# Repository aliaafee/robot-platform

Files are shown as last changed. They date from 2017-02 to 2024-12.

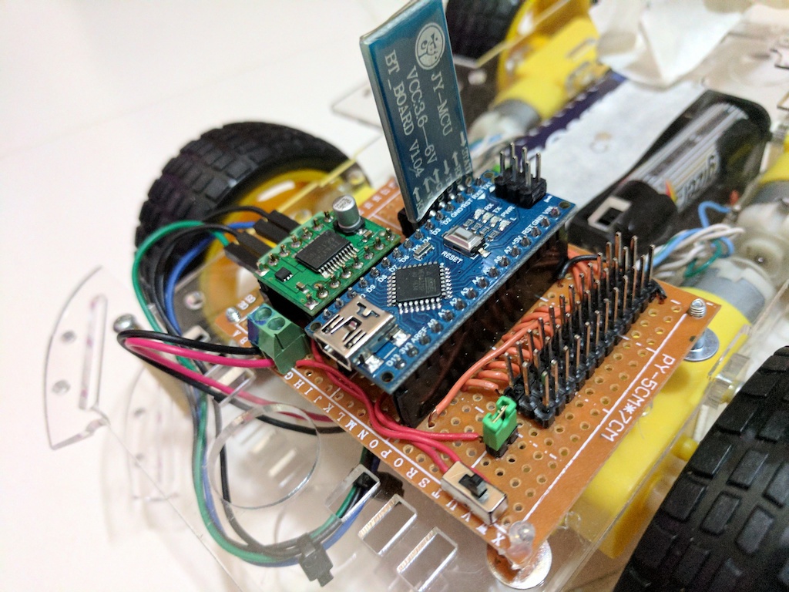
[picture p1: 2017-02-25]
photos/robot-platform.jpg

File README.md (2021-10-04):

# Robot Platform

An arduino based wheeled robot platform.

18650 battery holder

protection circuite
holder for two

2S 20A 7.4V w/Balance Lithium Li-ion 18650 Battery BMS Pack Protection PCB Board

LM2596 DC-DC Buck Converter Step Down Adjustable Power Supply Module

B0505S circuit isolator DC-DC converter

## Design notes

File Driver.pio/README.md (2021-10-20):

# Driver.pio

Firmware for robot driver.

TODO: Implement this as a finite state machine.
see http://robotics.sk/go/FSM/finite-state-automata.pdf

## Functions

Robot driver recieves commands over I2C bus(acts as I2C slave).
Performs basic functions such as movement and collision detection.
Acts as a state machine.

Example: when given command "move by x steps forward", 
sets internal state to "moving forward",
sets motor controller to move forwards,
starts counting steps using wheel encoder interrupts,
stops the motor and sets state to "stopped" when steps goal reached.
During this process robot driver is able to send status via I2C bus when
master makes a request. Robot driver also looks for collisions and stops
when collision detected and updates state appropriately and also sets an
error state.

## Build and Upload

* Install PlatformIO
* Install required depenencies `pio lib install`
* Update `board` and `upload_port` to appropriate values in `platformio.ini`
* Build `pio run`
* Upload to device `pio run -t upload`

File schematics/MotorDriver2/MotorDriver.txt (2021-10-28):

"Source:"	"/home/ali/Projects/robot-platform/schematics/MotorDriver2/MotorDriver.sch"
"Date:"	"Thu 28 Oct 2021 21:13:58 +0545"
"Tool:"	"Eeschema 5.1.10"
"Component Count:"	"37"
"Ref"	"Value"	"Part"	"Footprint"	"Description"	"Vendor"
"C1"	"10uF"	"Device:CP"	"Capacitor_SMD:CP_Elec_4x5.4"	"Polarized capacitor"	""
"C2"	"15pF"	"Device:C"	"Capacitor_SMD:C_1206_3216Metric"	"Unpolarized capacitor"	""
"C3"	"0.1uF"	"Device:C"	"Capacitor_SMD:C_1206_3216Metric"	"Unpolarized capacitor"	""
"C4"	"15pF"	"Device:C"	"Capacitor_SMD:C_1206_3216Metric"	"Unpolarized capacitor"	""
"C5"	"10uF"	"Device:CP"	"Capacitor_SMD:CP_Elec_4x5.4"	"Polarized capacitor"	""
"C6"	"0.1uF"	"Device:C"	"Capacitor_SMD:C_1206_3216Metric"	"Unpolarized capacitor"	""
"C7"	"0.1uF"	"Device:C"	"Capacitor_SMD:C_1206_3216Metric"	"Unpolarized capacitor"	""
"C8"	"0.1uf"	"Device:C"	"Capacitor_SMD:C_1206_3216Metric"	"Unpolarized capacitor"	""
"C9"	"10uf"	"Device:CP"	"Capacitor_SMD:CP_Elec_4x5.4"	"Polarized capacitor"	""
"C10"	"10uf"	"Device:CP"	"Capacitor_SMD:CP_Elec_4x5.4"	"Polarized capacitor"	""
"C11"	"0.1uf"	"Device:C"	"Capacitor_SMD:C_1206_3216Metric"	"Unpolarized capacitor"	""
"D1"	"RED"	"Device:LED"	"Diode_SMD:D_1206_3216Metric"	"Light emitting diode"	""
"D2"	"GREEN"	"Device:LED"	"Diode_SMD:D_1206_3216Metric"	"Light emitting diode"	""
"H1"	"MountingHole"	"Mechanical:MountingHole"	"MountingHole:MountingHole_2.5mm"	"Mounting Hole without connection"	""
"H2"	"MountingHole"	"Mechanical:MountingHole"	"MountingHole:MountingHole_2.5mm"	"Mounting Hole without connection"	""
"H3"	"MountingHole"	"Mechanical:MountingHole"	"MountingHole:MountingHole_2.5mm"	"Mounting Hole without connection"	""
"H4"	"MountingHole"	"Mechanical:MountingHole"	"MountingHole:MountingHole_2.5mm"	"Mounting Hole without connection"	""
"J1"	"9Vin"	"Connector_Generic:Conn_01x02"	"Connector_JST:JST_XH_B2B-XH-A_1x02_P2.50mm_Vertical"	"Generic connector, single row, 01x02, script generated (kicad-library-utils/schlib/autogen/connector/)"	""
"J2"	"ICSP"	"Connector_Generic:Conn_02x03_Odd_Even"	"Connector_PinHeader_2.54mm:PinHeader_2x03_P2.54mm_Vertical"	"Generic connector, double row, 02x03, odd/even pin numbering scheme (row 1 odd numbers, row 2 even numbers), script generated (kicad-library-utils/schlib/autogen/connector/)"	""
"J3"	"FTDI"	"Connector_Generic:Conn_01x06"	"Connector_PinHeader_2.54mm:PinHeader_1x06_P2.54mm_Vertical"	"Generic connector, single row, 01x06, script generated (kicad-library-utils/schlib/autogen/connector/)"	""
"J4"	"I2C"	"Connector_Generic:Conn_01x04"	"Connector_JST:JST_XH_B4B-XH-A_1x04_P2.50mm_Vertical"	"Generic connector, single row, 01x04, script generated (kicad-library-utils/schlib/autogen/connector/)"	""
"J5"	"3v3out"	"Connector_Generic:Conn_01x02"	"Connector_JST:JST_XH_B2B-XH-A_1x02_P2.50mm_Vertical"	"Generic connector, single row, 01x02, script generated (kicad-library-utils/schlib/autogen/connector/)"	""
"J6"	"AnalogPins"	"Connector_Generic:Conn_02x03_Odd_Even"	"Connector_PinHeader_2.54mm:PinHeader_2x03_P2.54mm_Vertical"	"Generic connector, double row, 02x03, odd/even pin numbering scheme (row 1 odd numbers, row 2 even numbers), script generated (kicad-library-utils/schlib/autogen/connector/)"	""
"J7"	"WheelEncA"	"Connector_Generic:Conn_01x03"	"Connector_JST:JST_XH_B3B-XH-A_1x03_P2.50mm_Vertical"	"Generic connector, single row, 01x03, script generated (kicad-library-utils/schlib/autogen/connector/)"	""
"J8"	"WheelEncB"	"Connector_Generic:Conn_01x03"	"Connector_JST:JST_XH_B3B-XH-A_1x03_P2.50mm_Vertical"	"Generic connector, single row, 01x03, script generated (kicad-library-utils/schlib/autogen/connector/)"	""
"J9"	"MotorA"	"Connector_Generic:Conn_01x02"	"Connector_JST:JST_XH_B2B-XH-A_1x02_P2.50mm_Vertical"	"Generic connector, single row, 01x02, script generated (kicad-library-utils/schlib/autogen/connector/)"	""
"J10"	"MotorB"	"Connector_Generic:Conn_01x02"	"Connector_JST:JST_XH_B2B-XH-A_1x02_P2.50mm_Vertical"	"Generic connector, single row, 01x02, script generated (kicad-library-utils/schlib/autogen/connector/)"	""
"R1"	"10k"	"Device:R"	"Resistor_SMD:R_1206_3216Metric"	"Resistor"	""
"R2"	"10k"	"Device:R"	"Resistor_SMD:R_1206_3216Metric"	"Resistor"	""
"R3"	"10k"	"Device:R"	"Resistor_SMD:R_1206_3216Metric"	"Resistor"	""
"R4"	"10k"	"Device:R"	"Resistor_SMD:R_1206_3216Metric"	"Resistor"	""
"R5"	"330"	"Device:R"	"Resistor_SMD:R_1206_3216Metric"	"Resistor"	""
"SW1"	"Reset"	"Switch:SW_Push"	"Button_Switch_SMD:SW_SPST_B3U-1000P-B"	"Push button switch, generic, two pins"	""
"U1"	"ATmega328P-MU"	"MCU_Microchip_ATmega:ATmega328P-MU"	"Package_DFN_QFN:QFN-32-1EP_5x5mm_P0.5mm_EP3.1x3.1mm"	"20MHz, 32kB Flash, 2kB SRAM, 1kB EEPROM, QFN-32"	""
"U2"	"MIC5205-3.3YM5"	"Regulator_Linear:MIC5205-3.3YM5"	"Package_TO_SOT_SMD:SOT-23-5"	"150mA low dropout linear regulator, fixed 3.3V output, SOT-23-5"	""
"U3"	"TB6612FNG"	"Driver_Motor:TB6612FNG"	"Package_SO:SSOP-24_5.3x8.2mm_P0.65mm"	"Driver IC for Dual DC motor, SSOP-24"	""
"Y1"	"HC-49SM16MHz20pF30ppm"	"Device:Crystal"	"Crystal:Crystal_SMD_HC49-SD"	"Two pin crystal"	""

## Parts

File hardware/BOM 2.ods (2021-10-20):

# | Desc | Qty | Unit Price | Price | Exclude | Remaining | Details
Power
1 | ICR 18650 Cell (Samsung) | 2 | 7.78 | 15.56 |  | 15.56
2 | 18650 Holder 2 Cell | 1 | 1.22 | 1.22 |  | 1.22
3 | 18650 BMS 2S 3A 7.4V | 1 | 0.42 | 0.42 |  | 0.42
4 | TP5100 Lithium Battery Charge Manager | 1 | 0.57 | 0.57 |  | 0.57
5 | Mini360 DC-DC Step Down Buck Converter | 2 | 0.42 | 0.83 |  | 0.83 | 3.3v and 5v output
6 | MT3608 DC-DC Step Up Boost Converter | 1 | 1.90 | 1.90 |  | 1.90 | 9v out for motor
Robot Driver
1 | Arduino Pro Mini 328 3.3v 8MHz | 1 | 2.69 | 2.69 |  | 2.69 | Brain for driver
2 | USB to TTL Serial Adapter | 1 | 1.21 | 1.21 |  | 1.21 | Programmer for arduino pro mini
3 | TB6612FNG Dual Motor Driver | 1 | 1.30 | 1.30 | 1 | 0.00
4 | HC-02K Speed Sensor Wheel Encoder | 2 | 0.97 | 1.94 |  | 1.94 | *Not needed if chassis available
5 | TCRT5000 Infrared Reflectance Sensor Analog | 4 | 0.71 | 2.84 |  | 2.84 | Front, Back, and Edge on Both Side
Robot Control
1 | Raspberry Pi Zero W | 1 | 14.00 | 14.00 | 1 | 0.00
2 | Triple Axis Compass/Magnetometer Module I2C | 1 | 1.61 | 1.61 |  | 1.61 | Direction
3 | Six Axis Gyro/Accelerometer Module I2C | 1 | 1.41 | 1.41 |  | 1.41 | Orientation
4 | Raspberry Pi Camera | 1 | 29.95 | 29.95 | 1 | 0.00 | Vision
5 | RC Servo – Micro 9G | 2 | 1.98 | 3.96 |  | 3.96 | For Camera Orientation
Robot Chassis
1 | TS100 Metal Tank Chassis with 9v 150rm Motor | 1 | 72.19 | 72.19 |  | 72.19
Communication
1 | 2 Channel I2C Logic Level Converter | 1 | 0.24 | 0.24 |  | 0.24 | For interfacing with 5v devices
Wiring
1 | Stripboard PCB | 3 | 1.40 | 4.20 |  | 4.20
2 | M3 Nylon Standoff kit | 1 | 3.36 | 3.36 |  | 3.36
3 | M3 Brass Standoff kit | 1 | 4.49 | 4.49 |  | 4.49
4 | M2.5 Nylon Standoff kit | 1 | 4.39 | 4.39 |  | 4.39
5 | M2.5 Brass Standoff kit | 1 | 4.99 | 4.99 |  | 4.99
6 | JST XH2.54 Wire Cable Crimmped with Female Plug Pins-4,3,2 | 5 | 0.76 | 3.80 |  | 3.80 | 4pin for I2C, 3pin for Analog/Digital Sensors, 2 pin for Power Delivery
 |  |  |  | 179.07 | Total(USD) | 133.82
 |  |  |  |  | MVR | 2063.5044

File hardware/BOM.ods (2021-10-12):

180Pcs/set M2 M2.5 M3 Hex Head Brass Spacing Screws Threaded Pillar PCB Computer PC Motherboard StandOff Spacer Kit B040
180Pcs/set M2 M2.5 M3 Hex Head Brass Spacing Screws Threaded Pillar PCB Computer PC Motherboard StandOff Spacer Kit B040
200Pcs/set M2 M2.5 M3 M4 Black/White Hex Nylon Standoff Spacer Column Flat Head Nylon Plastic Spacing Screws Nuts
200Pcs/set M2 M2.5 M3 M4 Black/White Hex Nylon Standoff Spacer Column Flat Head Nylon Plastic Spacing Screws Nuts
2SET HC-020K Double Speed Measuring Module to Test Motor's Rotational Speed with Photoelectric Encoders kit
2/4/8 Channel IIC I2C Logic Level Converter Bi-Directional Board Module 2 4 8 Way DC 3.3V/5V With Pins For Arduino Raspberry Pi
5PCS S09 DC-DC Automatic Buck Boost Power Step Up Down Board Module Input 3V-15V Output 3.3V/5V Electronic DIY PCB
5PCS MT3608 DC-DC Step Up Converter Booster Power Supply Module Boost Step-up Board MAX output 28V 2A
5pcs RC Airplane Module Mini 360 DC Buck Converter Step Down Module 4.75V-23V to 1V-17V 17x11x3.8mm New LM2596 2A
TS100 Metal Rc Robot Tank Car Chassis Shock Absorption Car With Suspension System Crawler Caterpillar For Arduino Diy Toy
5 Pcs 6.5x14.5cm Stripboard Veroboard Uncut PCB Platine Single Side Circuit Board
WAVGAT TB6612 DRV8833 Dual Motor Driver 1A TB6612FNG for Arduino Microcontroller Better than L298N
2S 3A 4A 5A 8A 10A 13A 20A 7.4V 8.4V Li-ion 18650 Lithium battery protection board / BMS board Standard / Balance | 18650 2S BMS 3A
1PCS 5V 1A Micro USB 18650 type-c Lithium Battery Charging Board Charger Module+Protection Dual Functions TP4056 18650
1 2 3 4 6 8 x AA High quality DIY Battery Holder Storage Case Box With Switch&Cover for 18650 AA Batteries Standard Container | 18650 size
Raspberry Pi Zero WH
Raspberry Pi NoIR Camera Board
Adjustable Pi Camera Mount
Raspberry Pi Zero v1.3 Camera Cable

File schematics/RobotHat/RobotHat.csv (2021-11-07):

Comment | Designator | Footprint | JLCPCB Part #
100uF | C1 | Capacitor_SMD:CP_Elec_6.3x7.7 | C127971
100nF | C3 | Capacitor_SMD:C_1206_3216Metric | C307331
220uf | C5 | Capacitor_SMD:CP_Elec_6.3x7.7 | C371974
100nF | C6 | Capacitor_SMD:C_1206_3216Metric | C307331
100nF | C7 | Capacitor_SMD:C_1206_3216Metric | C307331
10uf | C8 | Capacitor_SMD:CP_Elec_4x5.3 | C134721
100nF | C9 | Capacitor_SMD:C_1206_3216Metric | C307331
100nF | C10 | Capacitor_SMD:C_1206_3216Metric | C307331
100nF | C11 | Capacitor_SMD:C_1206_3216Metric | C307331
SS34 | D1 | RobotHat:SS34 | C8678
RED | D2 | Diode_SMD:D_0201_0603Metric | C2286
RED | D3 | Diode_SMD:D_0201_0603Metric | C2286
RED | D4 | Diode_SMD:D_0201_0603Metric | C2286
33uH | L1 | RobotHat:YPRH1207-330M | C339951
AO3401A | Q1 | Package_TO_SOT_SMD:SOT-23 | C15127
2N7002 | Q2 | Package_TO_SOT_SMD:SOT-23 | C8545
2N7002 | Q3 | Package_TO_SOT_SMD:SOT-23 | C8545
10k | R3 | Resistor_SMD:R_0201_0603Metric | C25804
330 | R4 | Resistor_SMD:R_0201_0603Metric | C23138
330 | R5 | Resistor_SMD:R_0201_0603Metric | C23138
330 | R6 | Resistor_SMD:R_0201_0603Metric | C23138
10k | R7 | Resistor_SMD:R_0201_0603Metric | C25804
10k | R8 | Resistor_SMD:R_0201_0603Metric | C25804
10k | R9 | Resistor_SMD:R_0201_0603Metric | C25804
10k | R10 | Resistor_SMD:R_0201_0603Metric | C25804
Reset | SW1 | MyFootprints:TS-1187A-B-A-B_PushButton | C318884
ATmega328P-AU | U1 | Package_QFP:TQFP-32_7x7mm_P0.8mm | C14877
LM2596S-5 | U2 | Package_TO_SOT_SMD:TO-263-5_TabPin3 | C194349
TB6612FNG | U3 | Package_SO:SSOP-24_5.3x8.2mm_P0.65mm | C141517
16Mhz | Y1 | RobotHat:CSTCE16M0V53-R0 | C32180

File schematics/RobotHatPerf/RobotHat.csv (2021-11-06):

Comment | Designator | Footprint | JLCPCB Part #
100uF | C1 | Capacitor_SMD:CP_Elec_6.3x7.7 | C127971
22pF | C2 | Capacitor_SMD:C_1206_3216Metric | C12891
22pF | C3 | Capacitor_SMD:C_1206_3216Metric | C12891
100nF | C4 | Capacitor_SMD:C_0402_1005Metric | C307331
220uf | C5 | Capacitor_SMD:CP_Elec_6.3x7.7 | C371974
100nF | C6 | Capacitor_SMD:C_0402_1005Metric | C307331
100nF | C7 | Capacitor_SMD:C_1206_3216Metric | C24497
100nF | C8 | Capacitor_SMD:C_1206_3216Metric | C24497
SS34 | D1 | RobotHat:SS34 | C8678
GREEN | D2 | Diode_SMD:D_0402_1005Metric | C130719
RED | D3 | Diode_SMD:D_0402_1005Metric | C130719
GREEN | D4 | Diode_SMD:D_0402_1005Metric | C130719
33uH | L1 | RobotHat:YPRH1207-330M | C339951
AO3401A | Q1 | Package_TO_SOT_SMD:SOT-23 | C15127
2N7002 | Q2 | Package_TO_SOT_SMD:SOT-23 | C8545
2N7002 | Q3 | Package_TO_SOT_SMD:SOT-23 | C8545
10k | R1 | Resistor_SMD:R_0805_2012Metric | C17724
330 | R3 | Resistor_SMD:R_0402_1005Metric | C25741
330 | R4 | Resistor_SMD:R_0402_1005Metric | C25741
10k | R5 | Resistor_SMD:R_0805_2012Metric | C17724
10k | R6 | Resistor_SMD:R_0805_2012Metric | C17724
10k | R7 | Resistor_SMD:R_0805_2012Metric | C17724
10k | R8 | Resistor_SMD:R_0805_2012Metric | C17724
Reset | SW1 | MyFootprints:TS-1187A-B-A-B_PushButton | C318884
LM2596S-5 | U2 | Package_TO_SOT_SMD:TO-263-5_TabPin3 | C194349

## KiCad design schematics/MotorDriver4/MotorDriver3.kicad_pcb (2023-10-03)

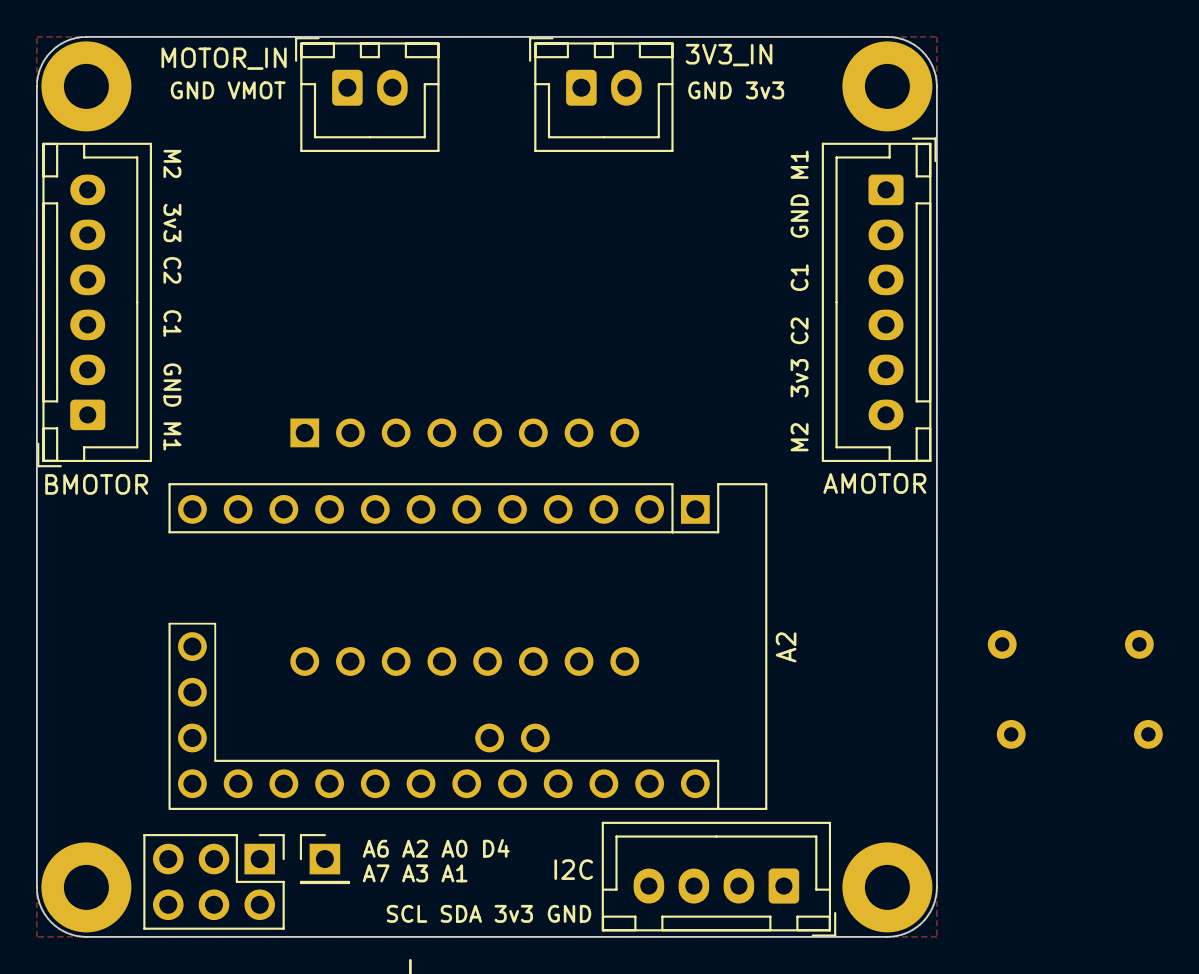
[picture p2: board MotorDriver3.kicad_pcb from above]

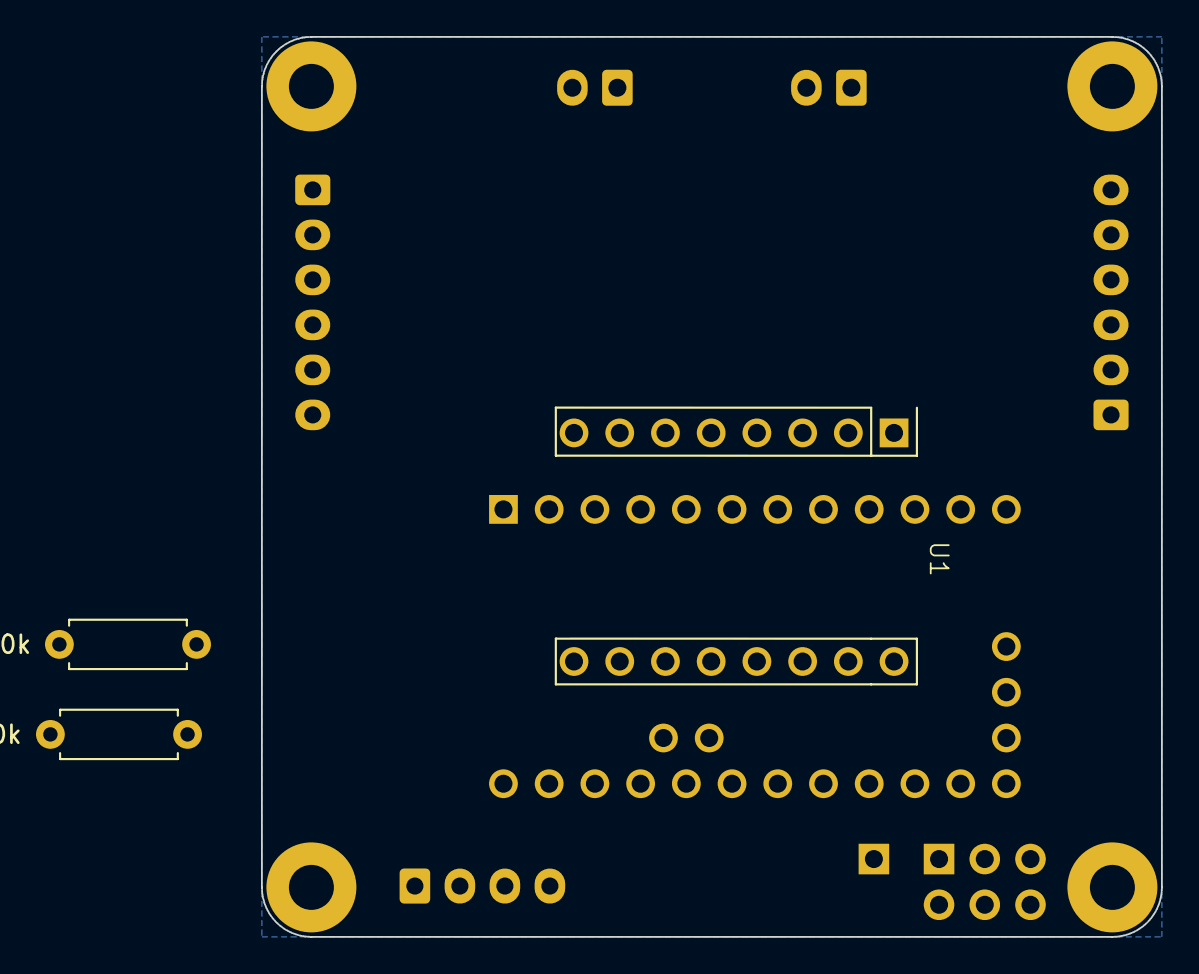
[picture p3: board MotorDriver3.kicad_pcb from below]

Board: 2 copper layers, 50.0 x 50.0 mm, 15 parts (3 on the bottom side), 27 nets, no tracks yet.

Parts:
A2: Arduino_Pro_Mini; Arduino Pro Mini
H1, H2, H3, H4: MountingHole_Pad; MountingHole_2.5mm_Pad
J1: AMOTOR; JST_XH_B6B-XH-A_1x06_P2.50mm_Vertical
J2: BMOTOR; JST_XH_B6B-XH-A_1x06_P2.50mm_Vertical
J3: I2C; JST_XH_B4B-XH-A_1x04_P2.50mm_Vertical
J4: AnalogPins; PinHeader_2x03_P2.54mm_Vertical
J5: MOTOR_IN; JST_XH_B2B-XH-A_1x02_P2.50mm_Vertical
J6: 3V3_IN; JST_XH_B2B-XH-A_1x02_P2.50mm_Vertical
J7: Digital Pins; PinHeader_1x01_P2.54mm_Vertical
R1, R2: 10k; R_Axial_DIN0207_L6.3mm_D2.5mm_P7.62mm_Horizontal
U1: TB6612FNG_Breakout; TB6612FBG_Breakout

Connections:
+3V3: A2.26 (VCC), J1.5, J2.5, J3.2, J6.2, R1.1, R2.1, U1.2 (VCC)
A0: A2.20 (A0), J4.1
A1: A2.21 (A1), J4.2
A2: A2.22 (A2), J4.3
A3: A2.23 (A3), J4.4
A6: A2.14 (A6), J4.5
A7: A2.15 (A7), J4.6
AIN1: A2.10 (D7), U1.15 (AIN2)
AIN2: A2.9 (D6), U1.14 (AIN1)
AINT1: A2.5 (D2), J1.3
AINT2: A2.18 (D12), J1.4
AO1: J1.1, U1.3 (AO1)
AO2: J1.6, U1.4 (AO2)
BIN1: A2.12 (D9), U1.12 (BIN1)
BIN2: A2.16 (D10), U1.11 (BIN2)
BINT1: A2.6 (D3), J2.3
BINT2: A2.19 (D13), J2.4
BO1: J2.1, U1.6 (BO1)
BO2: J2.6, U1.5 (BO2)
D4: A2.7 (D4), J7.1
GND: A2.4 (GND), A2.13 (GND), A2.28 (GND), J1.2, J2.2, J3.1, J5.1, J6.1, U1.1 (GND), U1.8 (GND), U1.9 (GND)
PWMA: A2.8 (D5), U1.16 (PWMA)
PWMB: A2.17 (D11), U1.10 (PWMB)
SCL: A2.25 (A5), J3.4, R1.2
SDA: A2.24 (A4), J3.3, R2.2
STBY: A2.11 (D8), U1.13 (STBY)
VMOT: J5.2, U1.7 (VMOT)

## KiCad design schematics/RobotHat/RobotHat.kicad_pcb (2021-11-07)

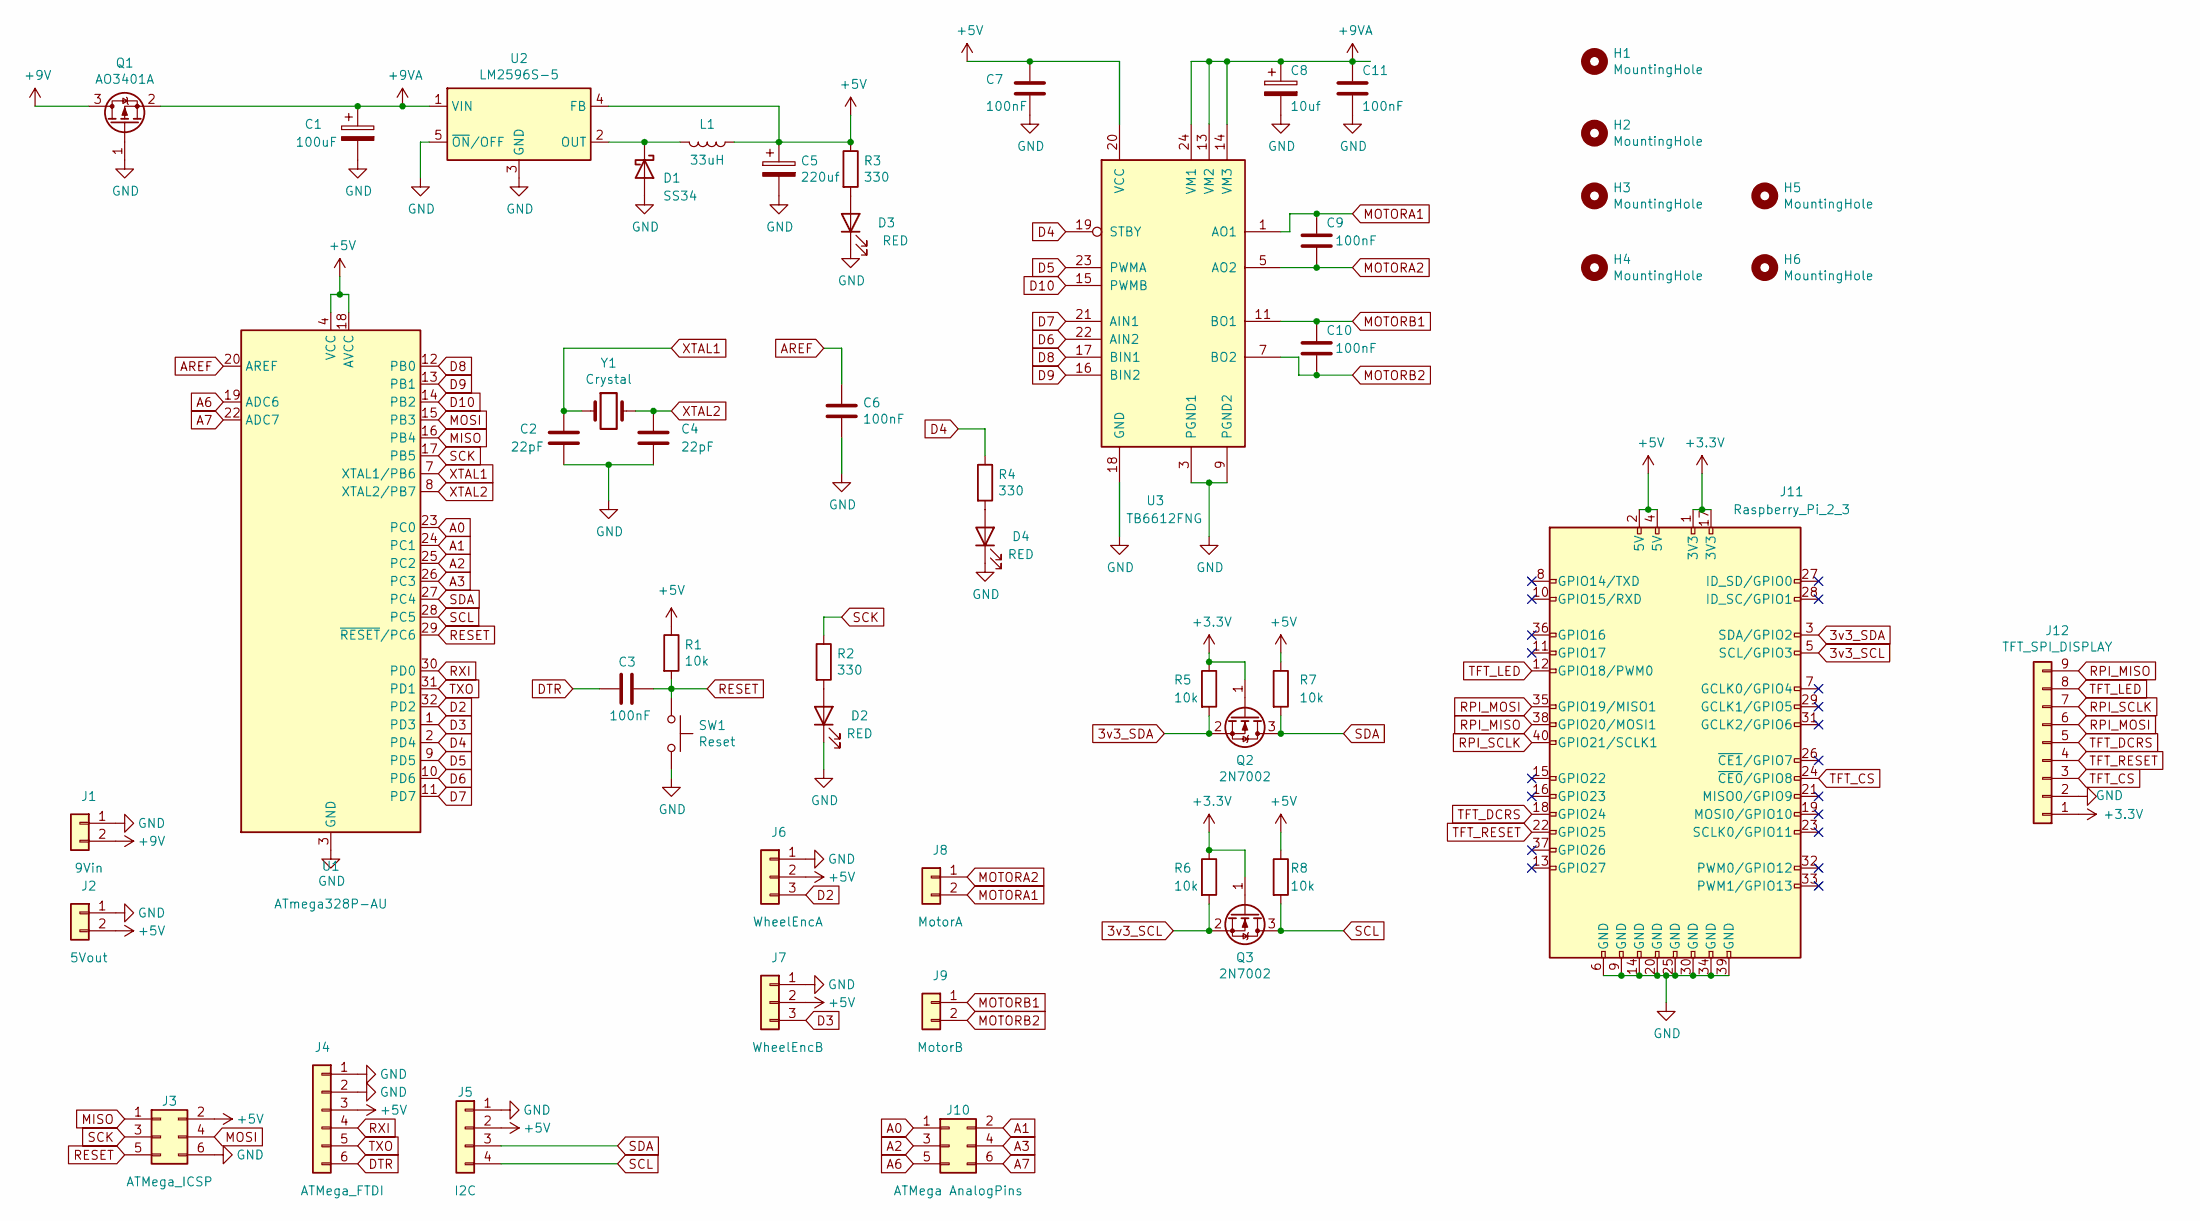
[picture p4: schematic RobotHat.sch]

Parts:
C1: 100uF; CP_Elec_6.3x7.7; Part C127971
C2, C4: 22pF; D_0603_1608Metric; Part C1653
C3, C6, C7, C11: 100nF; C_1206_3216Metric; Part C307331
C5: 220uf; CP_Elec_6.3x7.7; Part C371974
C8: 10uf; CP_Elec_4x5.3; Part C134721
C9, C10: 100nF; C_1206_3216Metric
D1: SS34; Part C8678
D2, D3, D4: RED; D_0603_1608Metric; Part C2286
H1, H2, H3, H4, H5, H6: MountingHole; MountingHole_2.7mm_M2.5_DIN965_Pad
J1: 9Vin; JST_XH_B2B-XH-A_1x02_P2.50mm_Vertical
J2: 5Vout; JST_XH_B2B-XH-A_1x02_P2.50mm_Vertical
J3: ATMega_ICSP; PinHeader_2x03_P2.54mm_Vertical
J4: ATMega_FTDI; PinHeader_1x06_P2.54mm_Horizontal
J5: I2C; JST_XH_B4B-XH-A_1x04_P2.50mm_Vertical
J6: WheelEncA; JST_XH_B3B-XH-A_1x03_P2.50mm_Vertical
J7: WheelEncB; JST_XH_B3B-XH-A_1x03_P2.50mm_Vertical
J8: MotorA; JST_XH_B2B-XH-A_1x02_P2.50mm_Vertical
J9: MotorB; JST_XH_B2B-XH-A_1x02_P2.50mm_Vertical
J10: ATMega AnalogPins; PinSocket_2x03_P2.54mm_Horizontal
J11: Raspberry_Pi_2_3; PinSocket_2x20_P2.54mm_Vertical
J12: TFT_SPI_DISPLAY; PinHeader_2x05_P2.54mm_Vertical
L1: 33uH; YPRH1207-330M; Part C339951
Q1: AO3401A; SOT-23; Part C15127
Q2, Q3: 2N7002; SOT-23; Part C8545
R1, R5, R6, R7, R8: 10k; R_0603_1608Metric; Part C25804
R2, R3, R4: 330; R_0603_1608Metric; Part C23138
SW1: Reset; TS-1187A-B-A-B_PushButton; Part C318884
U1: ATmega328P-AU; TQFP-32_7x7mm_P0.8mm; Part C14877
U2: LM2596S-5; TO-263-5_TabPin3; Part C194349
U3: TB6612FNG; SSOP-24_5.3x8.2mm_P0.65mm; Part C141517
Y1: Crystal; Crystal_HC49-4H_Vertical

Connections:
3v3_SCL: J11.5 (SCL/GPIO3), Q3.2 (S), R6.2
3v3_SDA: J11.3 (SDA/GPIO2), Q2.2 (S), R5.2
+3V3: J11.1 (3V3), J11.17 (3V3), J12.1, Q2.1 (G), Q3.1 (G), R5.1, R6.1
+5V: C5.1, C7.1, J2.2, J3.2, J4.3, J5.2, J6.2, J7.2, J11.2 (5V), J11.4 (5V), L1.1, R1.1, R3.1, R7.1, R8.1, U1.4 (VCC), U1.6 (VCC), U1.18 (AVCC), U2.4 (FB), U3.20 (VCC)
+9V: J1.2, Q1.3 (D)
+9VA: C1.1, C8.1, C11.1, Q1.2 (S), U2.1 (VIN), U3.13 (VM2), U3.14 (VM3), U3.24 (VM1)
A0: J10.1, U1.23 (PC0)
A1: J10.2, U1.24 (PC1)
A2: J10.3, U1.25 (PC2)
A3: J10.4, U1.26 (PC3)
A6: J10.5, U1.19 (ADC6)
A7: J10.6, U1.22 (ADC7)
AREF: C6.2, U1.20 (AREF)
D2: J6.3, U1.32 (PD2)
D3: J7.3, U1.1 (PD3)
D4: R4.1, U1.2 (PD4), U3.19 (STBY)
D5: U1.9 (PD5), U3.23 (PWMA)
D6: U1.10 (PD6), U3.22 (AIN2)
D7: U1.11 (PD7), U3.21 (AIN1)
D8: U1.12 (PB0), U3.17 (BIN1)
D9: U1.13 (PB1), U3.16 (BIN2)
D10: U1.14 (PB2), U3.15 (PWMB)
DTR: C3.1, J4.6
GND: C1.2, C2.2, C4.2, C5.2, C6.1, C7.2, C8.2, C11.2, D1.2 (A), D2.1 (K), D3.1 (K), D4.1 (K), J1.1, J2.1, J3.6, J4.1, J4.2, J5.1, J6.1, J7.1, J11.6 (GND), J11.9 (GND), J11.14 (GND), J11.20 (GND), J11.25 (GND), J11.30 (GND), J11.34 (GND), J11.39 (GND), J12.2, Q1.1 (G), SW1.2, U1.3 (GND), U1.5 (GND), U1.21 (GND), U2.3 (GND), U2.5 (~ON~/OFF), U3.3 (PGND1), U3.4 (PGND1), U3.9 (PGND2), U3.10 (PGND2), U3.18 (GND)
MISO: J3.1, U1.16 (PB4)
MOSI: J3.4, U1.15 (PB3)
MOTORA1: C9.1, J8.2, U3.1 (AO1), U3.2 (AO1)
MOTORA2: C9.2, J8.1, U3.5 (AO2), U3.6 (AO2)
MOTORB1: C10.1, J9.1, U3.11 (BO1), U3.12 (BO1)
MOTORB2: C10.2, J9.2, U3.7 (BO2), U3.8 (BO2)
unnamed: D1.1 (K), L1.2, U2.2 (OUT)
unnamed: D2.2 (A), R2.2
unnamed: D3.2 (A), R3.2
unnamed: D4.2 (A), R4.2
RESET: C3.2, J3.5, R1.2, SW1.1, U1.29 (~RESET~/PC6)
RPI_MISO: J11.38 (GPIO20/MOSI1), J12.9
RPI_MOSI: J11.35 (GPIO19/MISO1), J12.6
RPI_SCLK: J11.40 (GPIO21/SCLK1), J12.7
RXI: J4.4, U1.30 (PD0)
SCK: J3.3, R2.1, U1.17 (PB5)
SCL: J5.4, Q3.3 (D), R8.2, U1.28 (PC5)
SDA: J5.3, Q2.3 (D), R7.2, U1.27 (PC4)
TFT_CS: J11.24 (~CE0~/GPIO8), J12.3
TFT_DCRS: J11.18 (GPIO24), J12.5
TFT_LED: J11.12 (GPIO18/PWM0), J12.8
TFT_RESET: J11.22 (GPIO25), J12.4
TXO: J4.5, U1.31 (PD1)
XTAL1: C2.1, U1.7 (XTAL1/PB6), Y1.1
XTAL2: C4.1, U1.8 (XTAL2/PB7), Y1.2

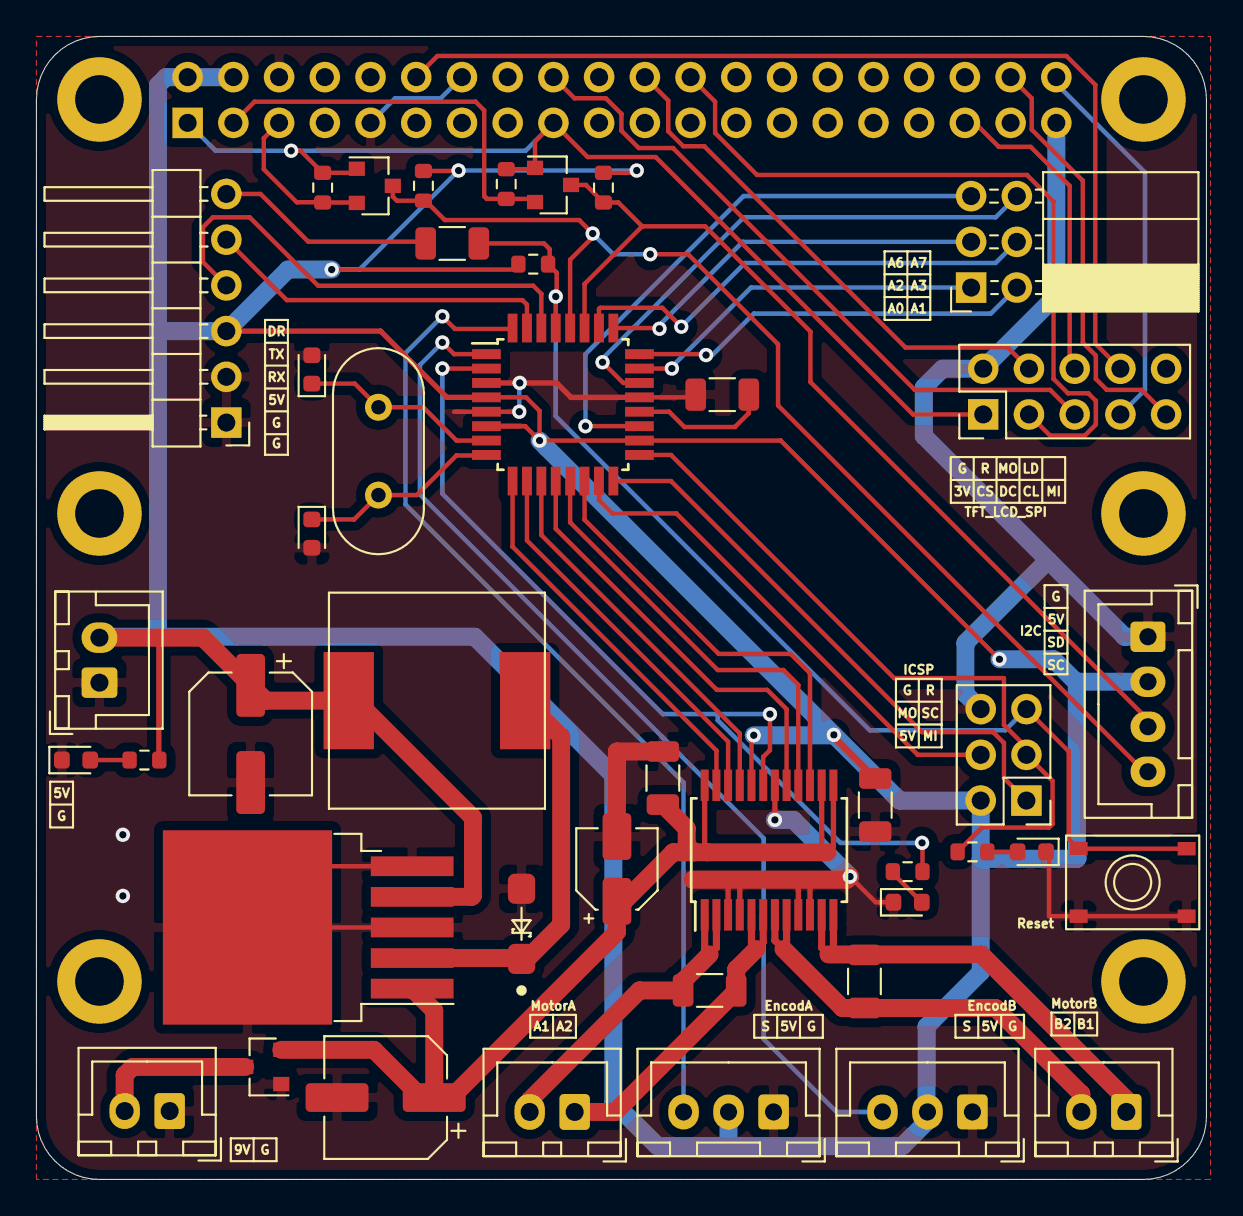
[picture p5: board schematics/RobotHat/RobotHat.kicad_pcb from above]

Board: 2 copper layers, 65.0 x 63.5 mm, 50 parts (1 on the bottom side), 49 nets.

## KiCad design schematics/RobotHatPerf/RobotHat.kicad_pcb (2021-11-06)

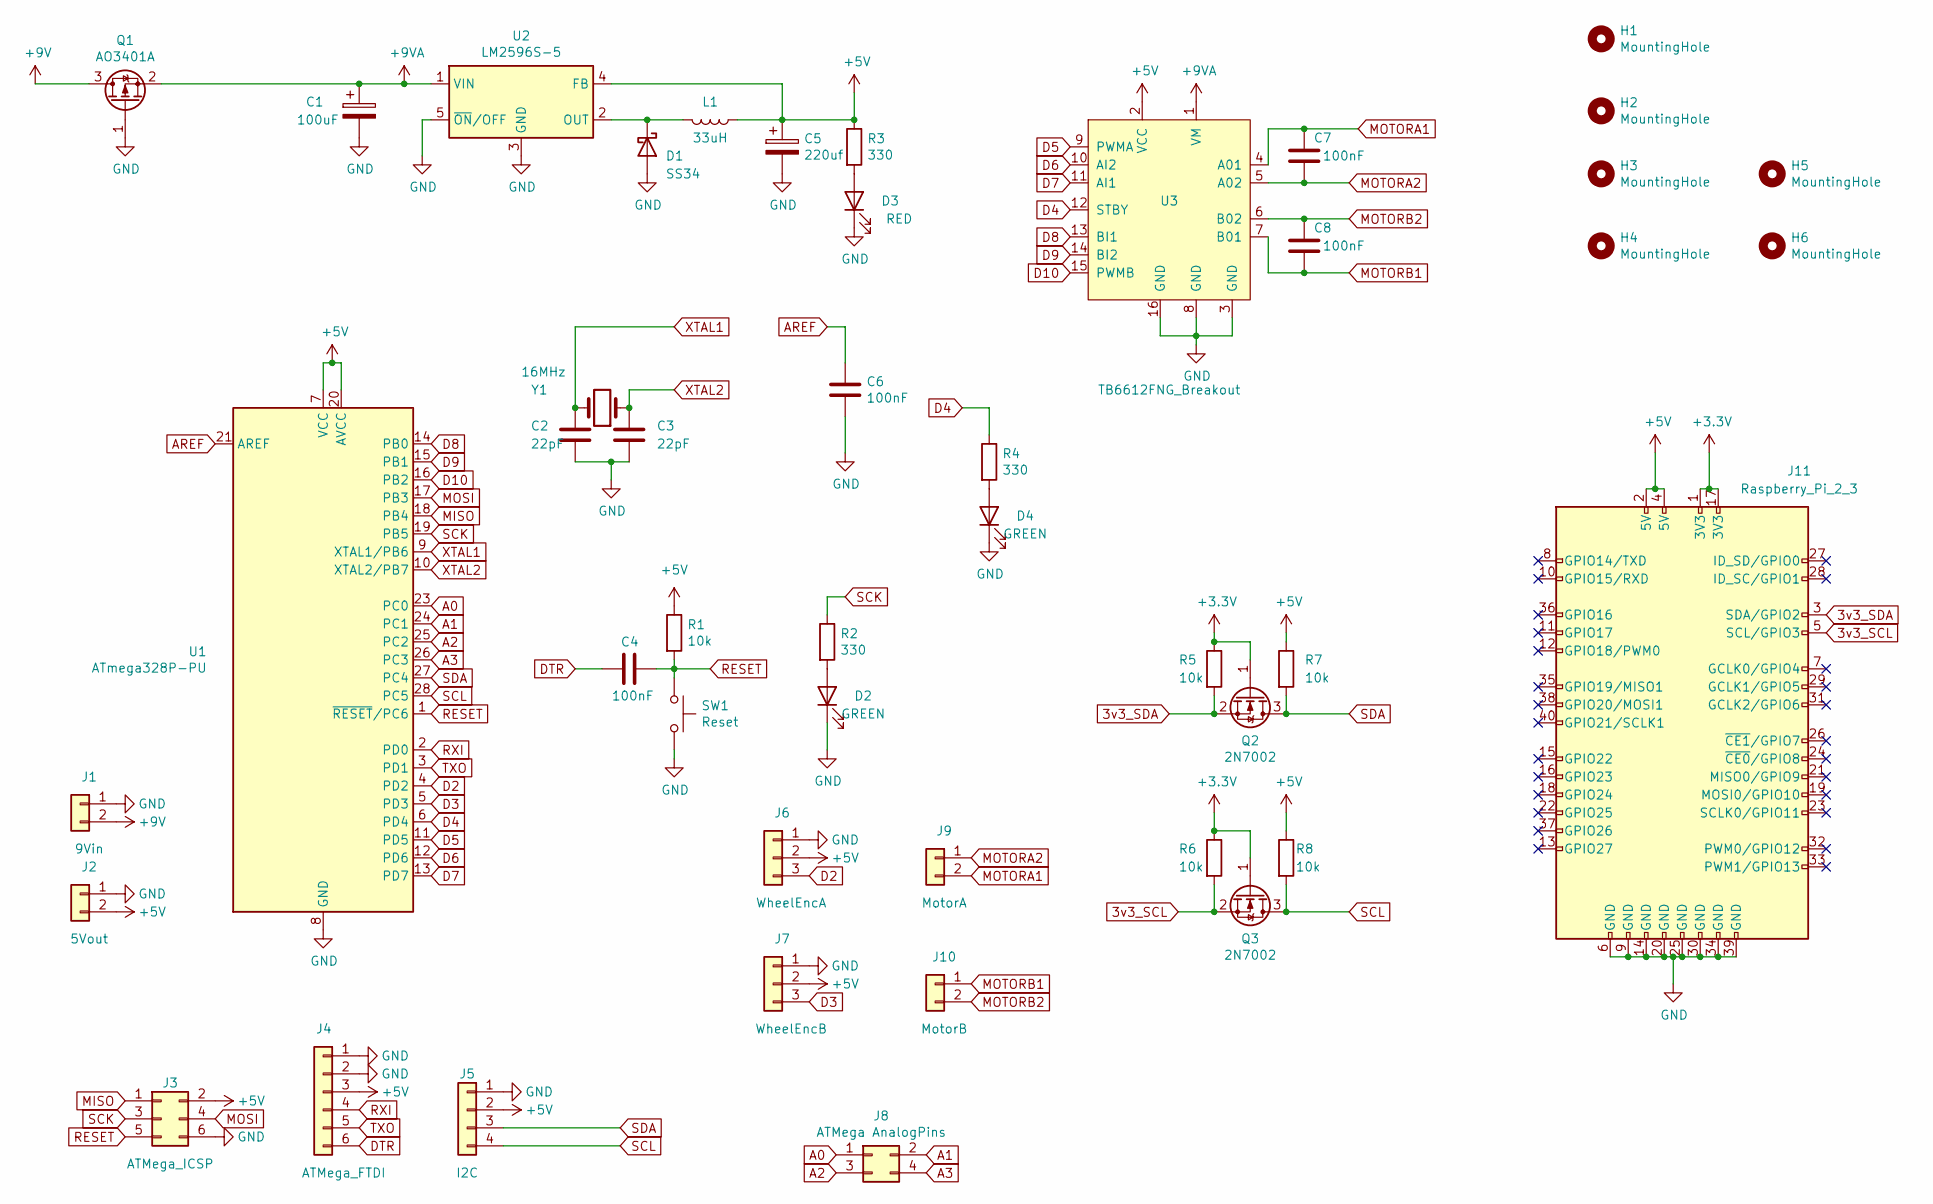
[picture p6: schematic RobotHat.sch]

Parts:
C1: 100uF; CP_Elec_6.3x7.7; Part C127971
C2, C3: 22pF; C_1206_3216Metric; Part C12891
C4, C6: 100nF; C_0402_1005Metric; Part C307331
C5: 220uf; CP_Elec_6.3x7.7; Part C371974
C7, C8: 100nF; C_1206_3216Metric; Part C24497
D1: SS34; Part C8678
D2, D4: GREEN; D_0402_1005Metric; Part C130719
D3: RED; D_0402_1005Metric; Part C130719
H1, H2, H3, H4, H5, H6: MountingHole; MountingHole_2.7mm_M2.5_DIN965_Pad
J1: 9Vin; JST_XH_B2B-XH-A_1x02_P2.50mm_Vertical
J2: 5Vout; JST_XH_B2B-XH-A_1x02_P2.50mm_Vertical
J3: ATMega_ICSP; PinHeader_2x03_P2.54mm_Vertical
J4: ATMega_FTDI; PinHeader_1x06_P2.54mm_Horizontal
J5: I2C; JST_XH_B4B-XH-A_1x04_P2.50mm_Vertical
J6: WheelEncA; JST_XH_B3B-XH-A_1x03_P2.50mm_Vertical
J7: WheelEncB; JST_XH_B3B-XH-A_1x03_P2.50mm_Vertical
J8: ATMega AnalogPins; PinSocket_1x04_P2.54mm_Horizontal
J9: MotorA; JST_XH_B2B-XH-A_1x02_P2.50mm_Vertical
J10: MotorB; JST_XH_B2B-XH-A_1x02_P2.50mm_Vertical
J11: Raspberry_Pi_2_3; PinSocket_2x20_P2.54mm_Vertical
L1: 33uH; YPRH1207-330M; Part C339951
Q1: AO3401A; SOT-23; Part C15127
Q2, Q3: 2N7002; SOT-23; Part C8545
R1, R5, R6, R7, R8: 10k; R_0805_2012Metric; Part C17724
R2, R3, R4: 330; R_0402_1005Metric; Part C25741
SW1: Reset; TS-1187A-B-A-B_PushButton; Part C318884
U1: ATmega328P-PU; DIP-28_W7.62mm
U2: LM2596S-5; TO-263-5_TabPin3; Part C194349
U3: TB6612FNG_Breakout
Y1: 16MHz; Crystal_HC49-U_Vertical

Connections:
3v3_SCL: J11.5 (SCL/GPIO3), Q3.2 (S), R6.2
3v3_SDA: J11.3 (SDA/GPIO2), Q2.2 (S), R5.2
+3V3: J11.1 (3V3), J11.17 (3V3), Q2.1 (G), Q3.1 (G), R5.1, R6.1
+5V: C5.1, J2.2, J3.2, J4.3, J5.2, J6.2, J7.2, J11.2 (5V), J11.4 (5V), L1.1, R1.1, R3.1, R7.1, R8.1, U1.7 (VCC), U1.20 (AVCC), U2.4 (FB), U3.2 (VCC)
+9V: J1.2, Q1.3 (D)
+9VA: C1.1, Q1.2 (S), U2.1 (VIN), U3.1 (VM)
A0: J8.1, U1.23 (PC0)
A1: J8.2, U1.24 (PC1)
A2: J8.3, U1.25 (PC2)
A3: J8.4, U1.26 (PC3)
AREF: C6.2, U1.21 (AREF)
D2: J6.3, U1.4 (PD2)
D3: J7.3, U1.5 (PD3)
D4: R4.1, U1.6 (PD4), U3.12 (STBY)
D5: U1.11 (PD5), U3.9 (PWMA)
D6: U1.12 (PD6), U3.10 (AI2)
D7: U1.13 (PD7), U3.11 (AI1)
D8: U1.14 (PB0), U3.13 (BI1)
D9: U1.15 (PB1), U3.14 (BI2)
D10: U1.16 (PB2), U3.15 (PWMB)
DTR: C4.1, J4.6
GND: C1.2, C2.2, C3.2, C5.2, C6.1, D1.2 (A), D2.1 (K), D3.1 (K), D4.1 (K), J1.1, J2.1, J3.6, J4.1, J4.2, J5.1, J6.1, J7.1, J11.6 (GND), J11.9 (GND), J11.14 (GND), J11.20 (GND), J11.25 (GND), J11.30 (GND), J11.34 (GND), J11.39 (GND), Q1.1 (G), SW1.2, U1.8 (GND), U1.22 (GND), U2.3 (GND), U2.5 (~ON~/OFF), U3.3 (GND), U3.8 (GND), U3.16 (GND)
MISO: J3.1, U1.18 (PB4)
MOSI: J3.4, U1.17 (PB3)
MOTORA1: C7.1, J9.2, U3.4 (A01)
MOTORA2: C7.2, J9.1, U3.5 (A02)
MOTORB1: C8.2, J10.1, U3.7 (B01)
MOTORB2: C8.1, J10.2, U3.6 (B02)
unnamed: D1.1 (K), L1.2, U2.2 (OUT)
unnamed: D2.2 (A), R2.2
unnamed: D3.2 (A), R3.2
unnamed: D4.2 (A), R4.2
RESET: C4.2, J3.5, R1.2, SW1.1, U1.1 (~RESET~/PC6)
RXI: J4.4, U1.2 (PD0)
SCK: J3.3, R2.1, U1.19 (PB5)
SCL: J5.4, Q3.3 (D), R8.2, U1.28 (PC5)
SDA: J5.3, Q2.3 (D), R7.2, U1.27 (PC4)
TXO: J4.5, U1.3 (PD1)
XTAL1: C2.1, U1.9 (XTAL1/PB6), Y1.2
XTAL2: C3.1, U1.10 (XTAL2/PB7), Y1.1

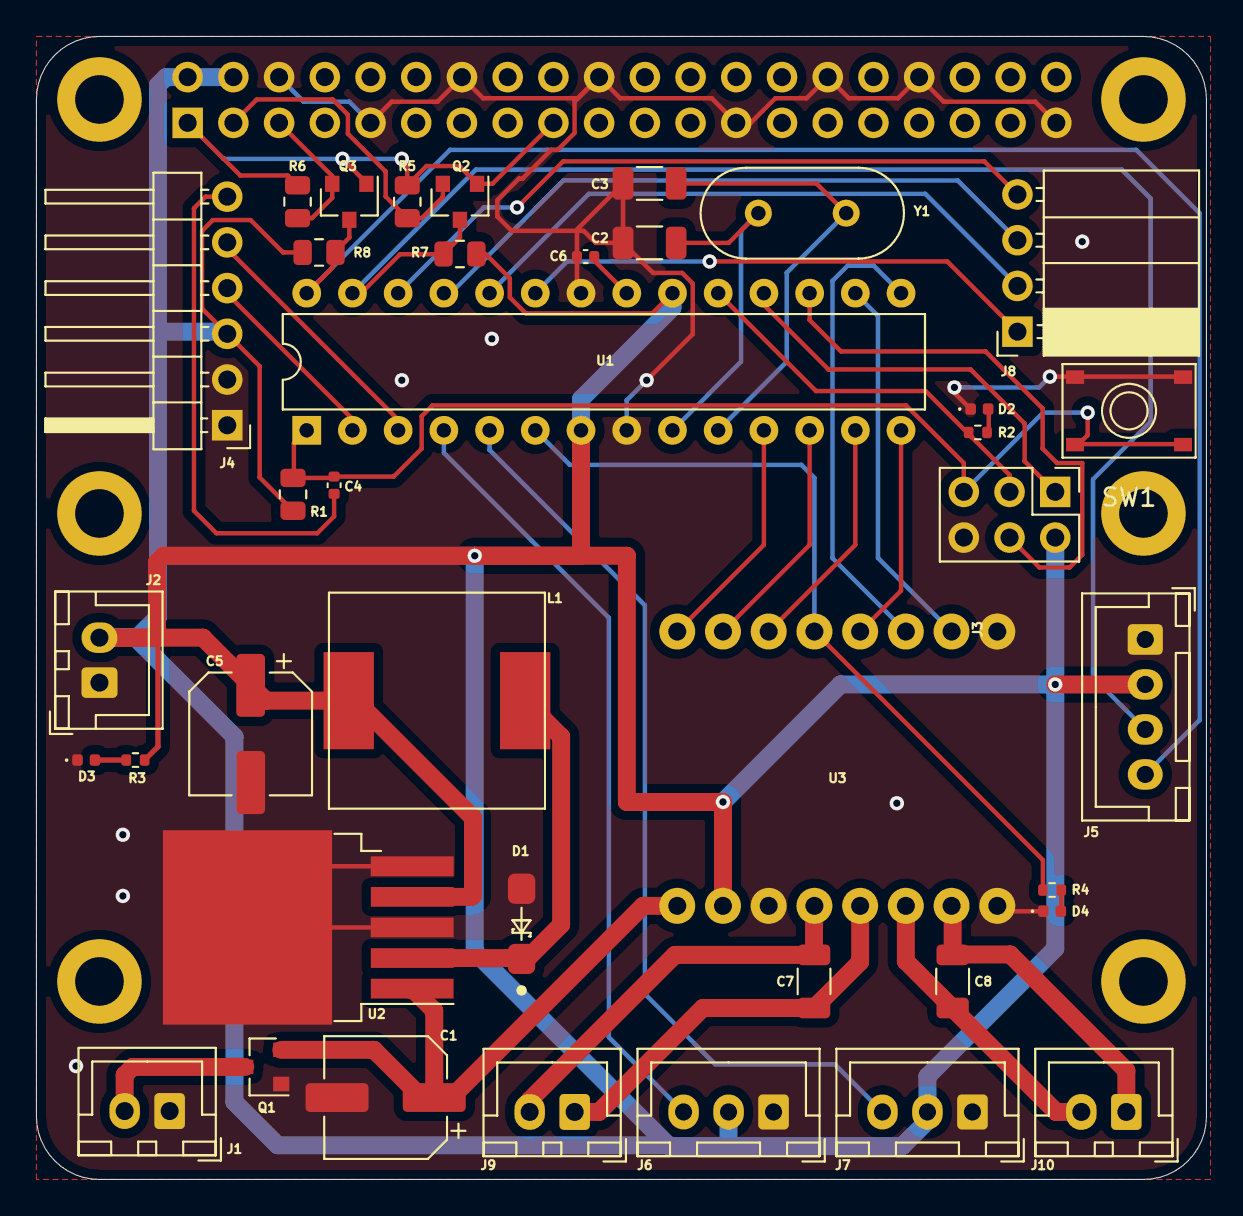
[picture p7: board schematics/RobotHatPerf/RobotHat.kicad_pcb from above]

Board: 2 copper layers, 65.0 x 63.5 mm, 46 parts (1 on the bottom side), 40 nets.

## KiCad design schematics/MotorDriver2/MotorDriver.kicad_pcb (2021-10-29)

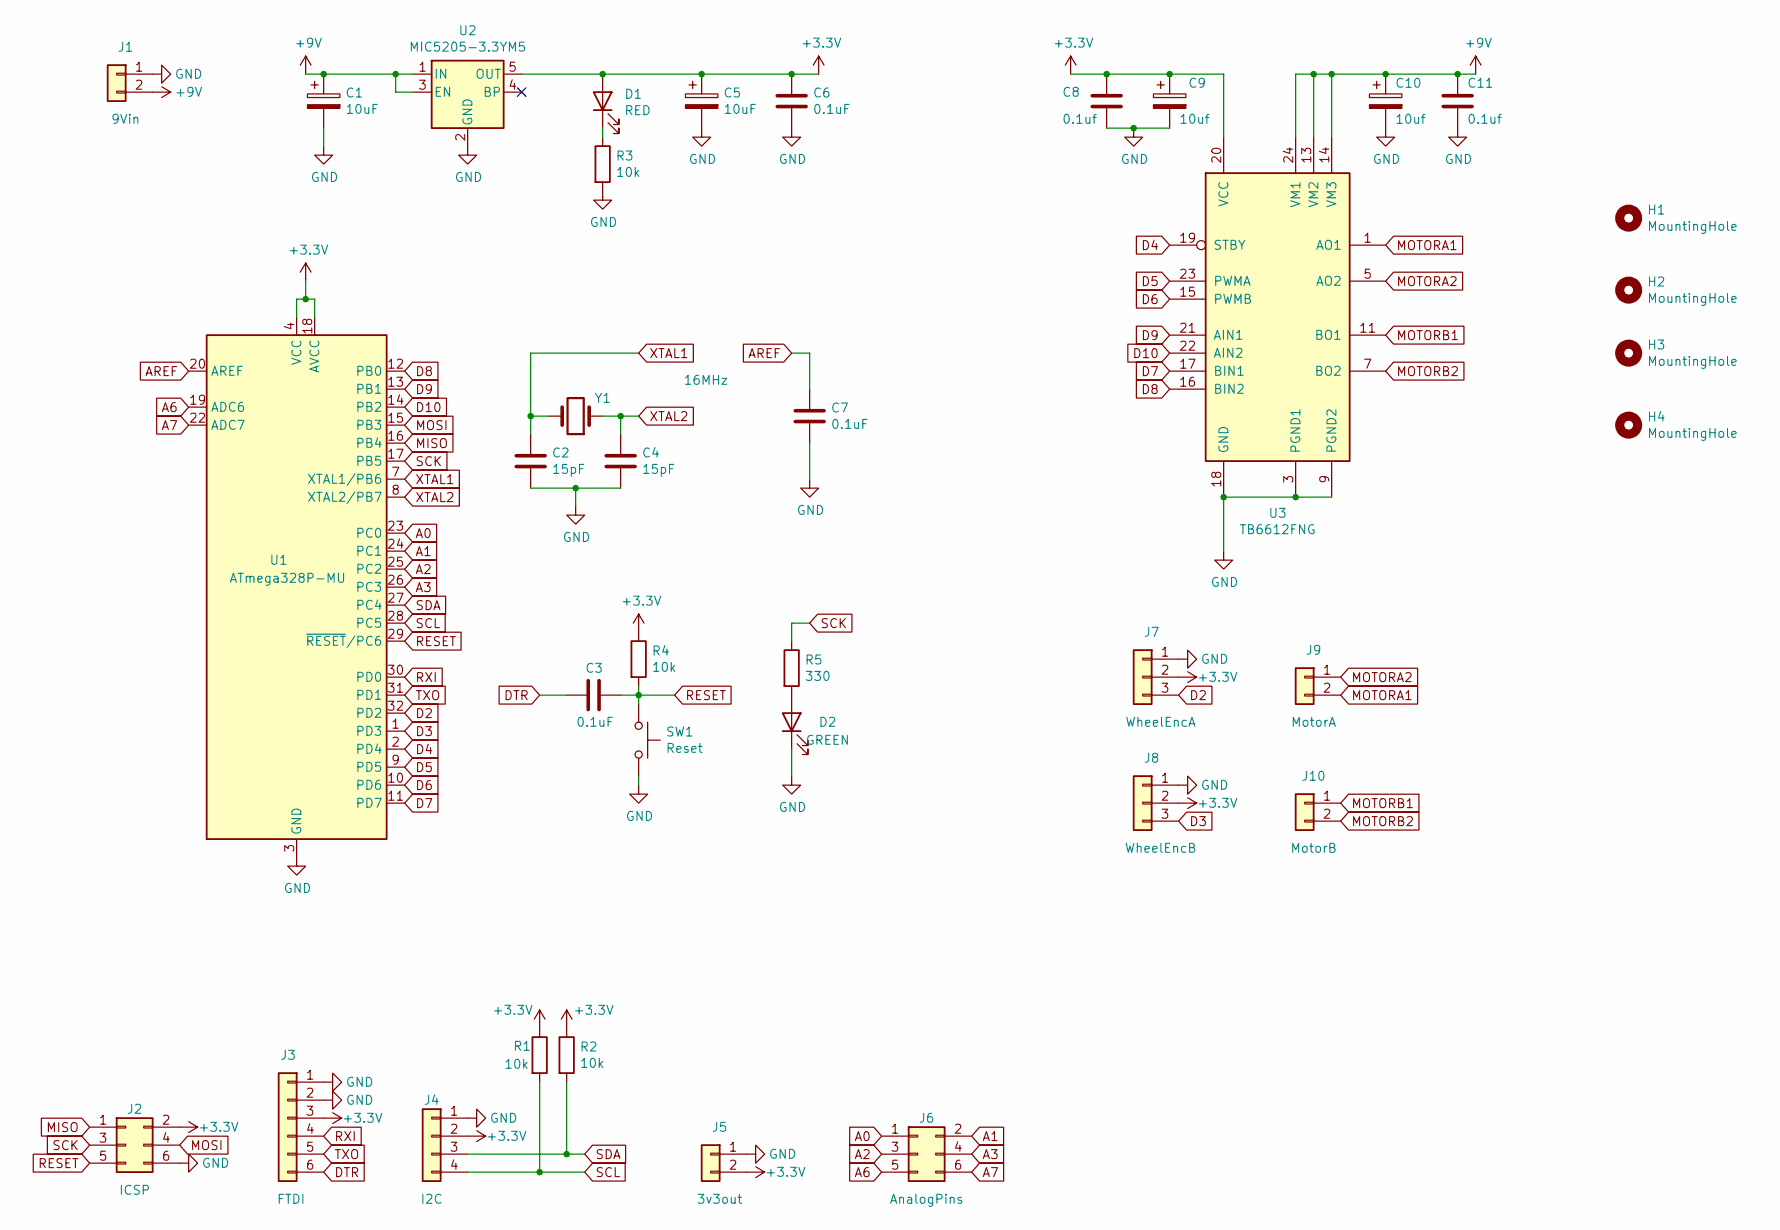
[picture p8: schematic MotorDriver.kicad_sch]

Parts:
C1, C5: 10uF; CP_Elec_4x5.4
C2, C4: 15pF; C_0402_1005Metric
C3, C6, C7: 0.1uF; C_0402_1005Metric
C8, C11: 0.1uf; C_0402_1005Metric
C9, C10: 10uf; CP_Elec_4x5.4
D1: RED; D_0402_1005Metric
D2: GREEN; D_0402_1005Metric
H1, H2, H3, H4: MountingHole; MountingHole_2.5mm
J1: 9Vin; JST_XH_B2B-XH-A_1x02_P2.50mm_Vertical
J2: ICSP; PinHeader_2x03_P2.54mm_Vertical
J3: FTDI; PinHeader_1x06_P2.54mm_Vertical
J4: I2C; JST_XH_B4B-XH-A_1x04_P2.50mm_Vertical
J5: 3v3out; JST_XH_B2B-XH-A_1x02_P2.50mm_Vertical
J6: AnalogPins; PinHeader_2x03_P2.54mm_Vertical
J7: WheelEncA; JST_XH_B3B-XH-A_1x03_P2.50mm_Vertical
J8: WheelEncB; JST_XH_B3B-XH-A_1x03_P2.50mm_Vertical
J9: MotorA; JST_XH_B2B-XH-A_1x02_P2.50mm_Vertical
J10: MotorB; JST_XH_B2B-XH-A_1x02_P2.50mm_Vertical
R1, R2, R3, R4: 10k; R_0402_1005Metric
R5: 330; R_0402_1005Metric
SW1: Reset; SW_SPST_B3U-1000P-B
U1: ATmega328P-MU; QFN-32-1EP_5x5mm_P0.5mm_EP3.1x3.1mm
U2: MIC5205-3.3YM5; SOT-23-5
U3: TB6612FNG; SSOP-24_5.3x8.2mm_P0.65mm
Y1: 16MHz; Crystal_SMD_HC49-SD

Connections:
+3V3: C5.1, C6.1, C8.1, C9.1, D1.2 (A), J2.2, J3.3, J4.2, J5.2, J7.2, J8.2, R1.1, R2.1, R4.1, U1.4 (VCC), U1.6 (VCC), U1.18 (AVCC), U2.5 (OUT), U3.20 (VCC)
+9V: C1.1, C10.1, C11.1, J1.2, U2.1 (IN), U2.3 (EN), U3.13 (VM2), U3.14 (VM3), U3.24 (VM1)
A0: J6.1, U1.23 (PC0)
A1: J6.2, U1.24 (PC1)
A2: J6.3, U1.25 (PC2)
A3: J6.4, U1.26 (PC3)
A6: J6.5, U1.19 (ADC6)
A7: J6.6, U1.22 (ADC7)
AREF: C7.2, U1.20 (AREF)
D2: J7.3, U1.32 (PD2)
D3: J8.3, U1.1 (PD3)
D4: U1.2 (PD4), U3.19 (STBY)
D5: U1.9 (PD5), U3.23 (PWMA)
D6: U1.10 (PD6), U3.15 (PWMB)
D7: U1.11 (PD7), U3.17 (BIN1)
D8: U1.12 (PB0), U3.16 (BIN2)
D9: U1.13 (PB1), U3.21 (AIN1)
D10: U1.14 (PB2), U3.22 (AIN2)
DTR: C3.1, J3.6
GND: C1.2, C2.1, C4.1, C5.2, C6.2, C7.1, C8.2, C9.2, C10.2, C11.2, D2.1 (K), J1.1, J2.6, J3.1, J3.2, J4.1, J5.1, J7.1, J8.1, R3.2, SW1.2, U1.3 (GND), U1.5 (GND), U1.21 (GND), U1.33 (GND), U2.2 (GND), U3.3 (PGND1), U3.4 (PGND1), U3.9 (PGND2), U3.10 (PGND2), U3.18 (GND)
MISO: J2.1, U1.16 (PB4)
MOSI: J2.4, U1.15 (PB3)
MOTORA1: J9.2, U3.1 (AO1), U3.2 (AO1)
MOTORA2: J9.1, U3.5 (AO2), U3.6 (AO2)
MOTORB1: J10.1, U3.11 (BO1), U3.12 (BO1)
MOTORB2: J10.2, U3.7 (BO2), U3.8 (BO2)
unnamed: D1.1 (K), R3.1
unnamed: D2.2 (A), R5.2
RESET: C3.2, J2.5, R4.2, SW1.1, U1.29 (~RESET/PC6)
RXI: J3.4, U1.30 (PD0)
SCK: J2.3, R5.1, U1.17 (PB5)
SCL: J4.4, R1.2, U1.28 (PC5)
SDA: J4.3, R2.2, U1.27 (PC4)
TXO: J3.5, U1.31 (PD1)
XTAL1: C2.2, U1.7 (XTAL1/PB6), Y1.2
XTAL2: C4.2, U1.8 (XTAL2/PB7), Y1.1

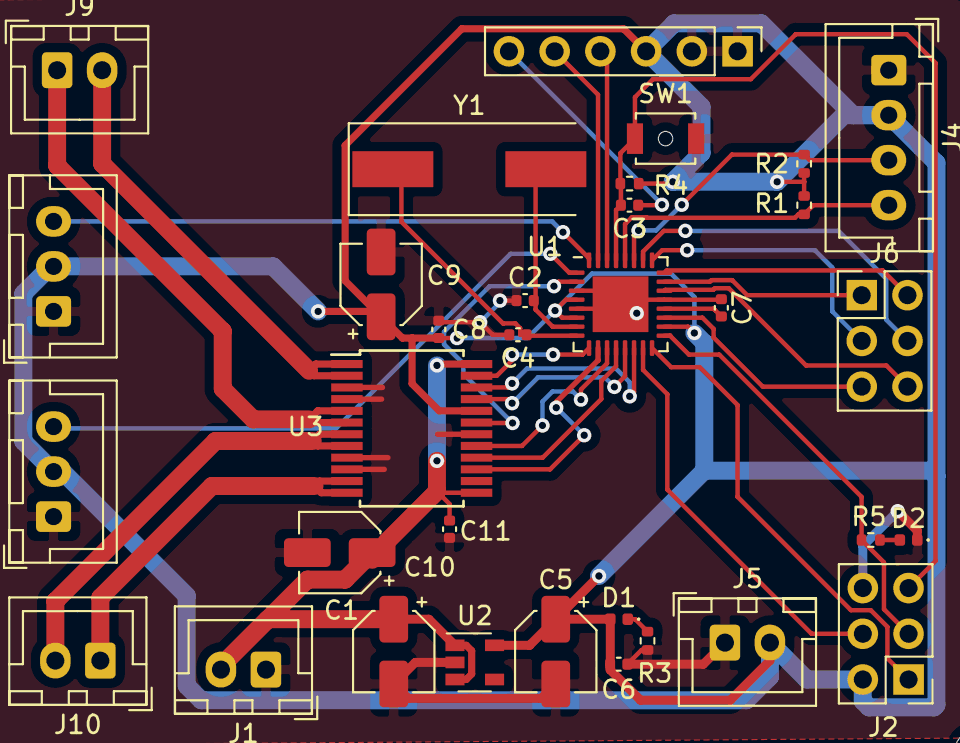
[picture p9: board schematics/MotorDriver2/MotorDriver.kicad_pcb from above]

Board: 2 copper layers, 37 parts (0 on the bottom side), 36 nets.

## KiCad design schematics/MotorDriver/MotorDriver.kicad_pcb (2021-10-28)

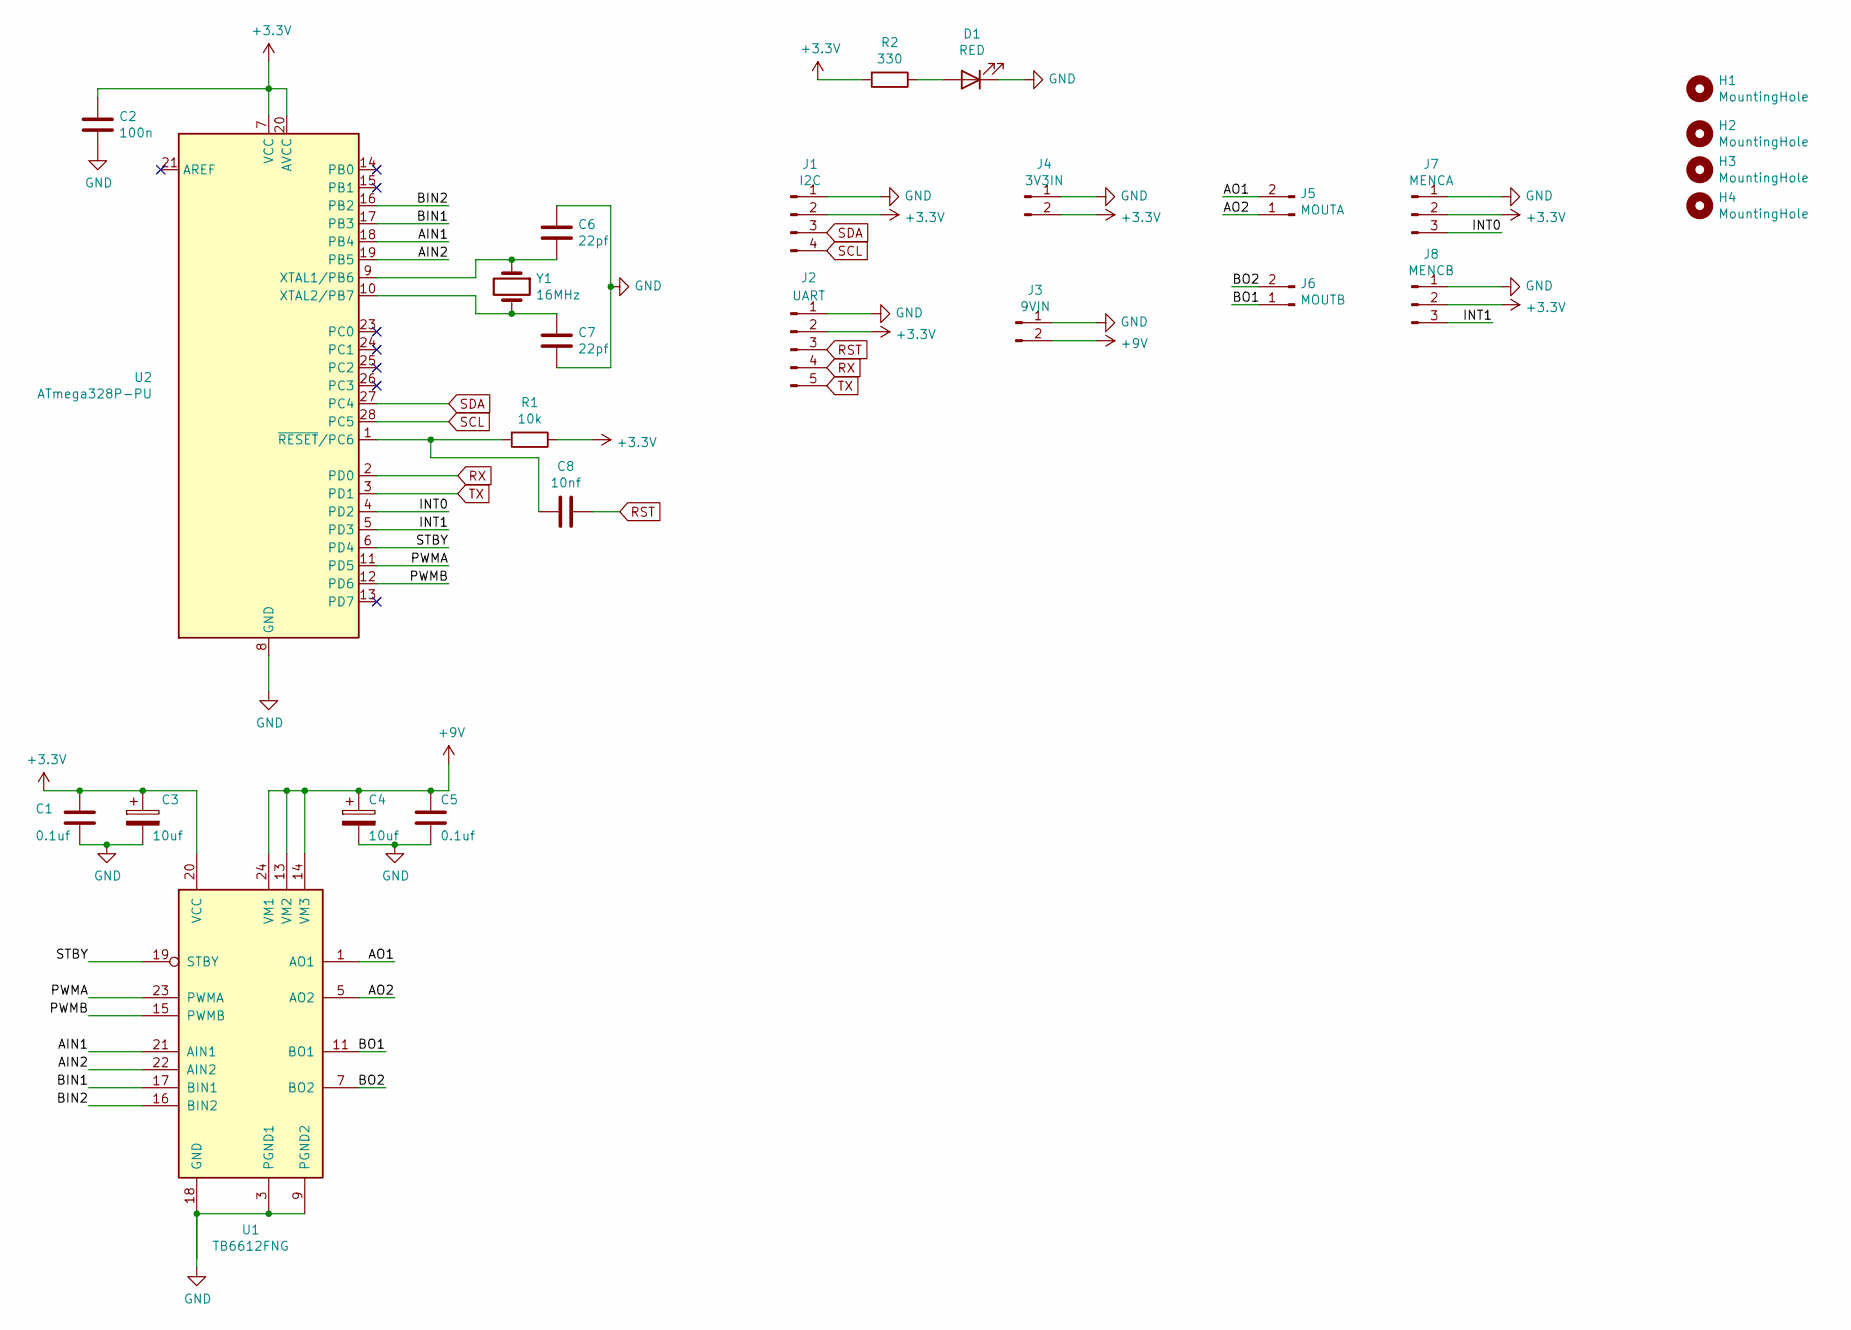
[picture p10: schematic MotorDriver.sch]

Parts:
C1, C5: 0.1uf; C_1206_3216Metric
C2: 100n; C_1206_3216Metric
C3, C4: 10uf; CP_Elec_3x5.3
C6, C7: 22pf; C_1206_3216Metric
C8: 10nf; C_1206_3216Metric
D1: RED; LED_1206_3216Metric
H1, H2, H3, H4: MountingHole; MountingHole_2.5mm_Pad_TopBottom
J1: I2C; JST_XH_B4B-XH-A_1x04_P2.50mm_Vertical
J2: UART; PinHeader_1x05_P2.54mm_Vertical
J3: 9VIN; JST_XH_B2B-XH-A_1x02_P2.50mm_Vertical
J4: 3V3IN; JST_XH_B2B-XH-A_1x02_P2.50mm_Vertical
J5: MOUTA; JST_XH_B2B-XH-A_1x02_P2.50mm_Vertical
J6: MOUTB; JST_XH_B2B-XH-A_1x02_P2.50mm_Vertical
J7: MENCA; JST_XH_B3B-XH-A_1x03_P2.50mm_Vertical
J8: MENCB; JST_XH_B3B-XH-A_1x03_P2.50mm_Vertical
R1: 10k; R_1206_3216Metric
R2: 330; R_1206_3216Metric
U1: TB6612FNG; SSOP-24_5.3x8.2mm_P0.65mm
U2: ATmega328P-PU; DIP-28_W7.62mm
Y1: 16MHz; Crystal_HC49-4H_Vertical

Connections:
+3V3: C1.1, C2.2, C3.1, J1.2, J2.2, J4.2, J7.2, J8.2, R1.1, R2.2, U1.20 (VCC), U2.7 (VCC), U2.20 (AVCC)
+9V: C4.1, C5.1, J3.2, U1.13 (VM2), U1.14 (VM3), U1.24 (VM1)
/AIN1: U1.21 (AIN1), U2.18 (PB4)
/AIN2: U1.22 (AIN2), U2.19 (PB5)
/AO1: J5.2, U1.1 (AO1), U1.2 (AO1)
/AO2: J5.1, U1.5 (AO2), U1.6 (AO2)
/BIN1: U1.17 (BIN1), U2.17 (PB3)
/BIN2: U1.16 (BIN2), U2.16 (PB2)
/BO1: J6.1, U1.11 (BO1), U1.12 (BO1)
/BO2: J6.2, U1.7 (BO2), U1.8 (BO2)
/INT0: J7.3, U2.4 (PD2)
/INT1: J8.3, U2.5 (PD3)
/PWMA: U1.23 (PWMA), U2.11 (PD5)
/PWMB: U1.15 (PWMB), U2.12 (PD6)
/STBY: U1.19 (STBY), U2.6 (PD4)
GND: C1.2, C2.1, C3.2, C4.2, C5.2, C6.2, C7.2, D1.1 (K), J1.1, J2.1, J3.1, J4.1, J7.1, J8.1, U1.3 (PGND1), U1.4 (PGND1), U1.9 (PGND2), U1.10 (PGND2), U1.18 (GND), U2.8 (GND), U2.22 (GND)
unnamed: C6.1, U2.9 (XTAL1/PB6), Y1.1
unnamed: C7.1, U2.10 (XTAL2/PB7), Y1.2
unnamed: C8.2, R1.2, U2.1 (~RESET~/PC6)
unnamed: D1.2 (A), R2.1
RST: C8.1, J2.3
RX: J2.4, U2.2 (PD0)
SCL: J1.4, U2.28 (PC5)
SDA: J1.3, U2.27 (PC4)
TX: J2.5, U2.3 (PD1)

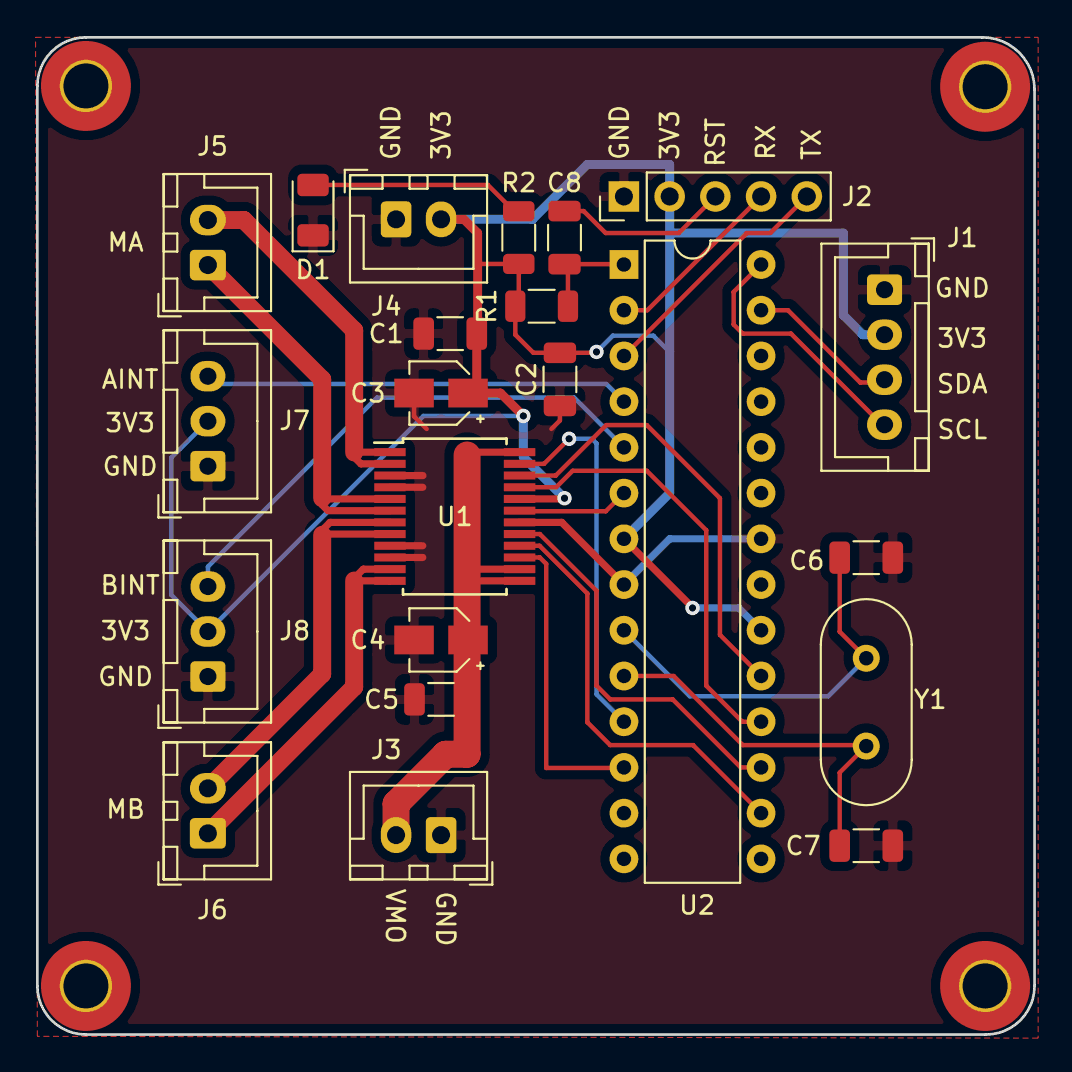
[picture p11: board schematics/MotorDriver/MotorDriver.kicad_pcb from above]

Board: 2 copper layers, 55.4 x 55.4 mm, 26 parts (0 on the bottom side), 25 nets.

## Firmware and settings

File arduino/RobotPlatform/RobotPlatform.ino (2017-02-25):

#include <Wire.h>
#include <LiquidCrystal_I2C.h>


class RobotPlatform
{
  public:
    RobotPlatform();
    void setup();
    void loop();
    bool processCommand();
    bool sendResponse();
  protected:
    String command;
    String previousCommand;
    String response;
    int deviceID;
    int commandLength;
    bool readLine(); //reads till \n or end of buffer.

    void setMotor(int motor, int speed, int direction);

    int motorLinearSpeed;
    int motorTurnSpeed;
    
    int STBY;
    int PWMA;
    int AIN1;
    int AIN2;
    int PWMB;
    int BIN1;
    int BIN2;

    LiquidCrystal_I2C *lcd;
};


RobotPlatform::RobotPlatform()
{
  deviceID = 1;
  commandLength = 10;
  command = "";
  response = "";

  PWMB = 11;
  BIN2 = 10;
  BIN1 = 9;
  
  STBY = 8;
  
  AIN1 = 7;
  AIN2 = 6;
  PWMA = 5;
  

  motorLinearSpeed = 75;
  motorTurnSpeed = 100;

  lcd = new LiquidCrystal_I2C(0x27, 2, 1, 0, 4, 5, 6, 7, 3, POSITIVE);
}

bool RobotPlatform::readLine()
{
  while (Serial.available()) {
    char lastByte = Serial.read();
    if (lastByte == '\n') {
      return true;
    }
    command += String(lastByte);
  }
  return false;
}

void RobotPlatform::setup()
{
  pinMode(STBY, OUTPUT);

  pinMode(PWMA, OUTPUT);
  pinMode(AIN1, OUTPUT);
  pinMode(AIN2, OUTPUT);

  pinMode(PWMB, OUTPUT);
  pinMode(BIN1, OUTPUT);
  pinMode(BIN2, OUTPUT);
  
  Serial.begin(9600);

  lcd->begin(16,2);
}

bool RobotPlatform::processCommand()
{
  String msg;
  
  response = "R";
  
  switch (command[0]) {
    case 'f':
      setMotor(0, motorLinearSpeed, 1);
      setMotor(1, motorLinearSpeed, 1);
      break;
      
    case 'b':
      setMotor(0, motorLinearSpeed, 0);
      setMotor(1, motorLinearSpeed, 0);
      break;
      
    case 'r':
      setMotor(0, motorTurnSpeed, 1);
      setMotor(1, motorTurnSpeed, 0);
      break;
      
    case 'l':
      setMotor(0, motorTurnSpeed, 0);
      setMotor(1, motorTurnSpeed, 1);
      break;
      
    case 's':
      setMotor(0, 0, 0);
      setMotor(1, 0, 0);
      break;

    case 'm':
      msg = command.substring(1);
      lcd->setCursor(0,0);
      lcd->print(msg);
      
    case 'd':
      /* Set Differential Speed
       *  0 - d
       *  1 - right wheel direction 1 forward, 0 back
       *  2 - right wheel speed 0-255
       *  3 - left wheel direction 1 forward, 0 back
       *  4 - left wheel speed 0-255
       */
      if (command.length() != 5) {
        return false;
      }
      int rd,rs,ld,ls;
      
      rd = (int(char(command[1])) == 0) ? 0 : 1;
      rs = int(char(command[2]));
      ld = (int(char(command[3])) == 0) ? 0 : 1;
      ls = int(char(command[4]));

      setMotor(0, ls, ld);
      setMotor(1, rs, rd);

      response += " ";
      response += String(rd);
      response += " ";
      response += String(rs);
      response += " ";
      response += String(ld);
      response += " ";
      response += String(ls);
      break;

    case 'c':
      /* read collision detection sensor */

      int v;
      v = analogRead(0);

      response += " ";
      response += String(v);
      
    default:
      return false;
  }

  return true;
}


bool RobotPlatform::sendResponse()
{
  response += " ";
  response += command;
  response += " ";
  response += String(millis());
  
  Serial.println(response);
  return 0;
}


void RobotPlatform::setMotor(int motor, int speed, int direction) {
  digitalWrite(STBY, HIGH);

  boolean inPin1 = LOW;
  boolean inPin2 = HIGH;

  if (direction == 1) {
    inPin1 = HIGH;
    inPin2 = LOW;
  }

  if (motor == 1) {
    digitalWrite(BIN1, inPin1);
    digitalWrite(BIN2, inPin2);
    analogWrite(PWMB, speed);
  } else {
    digitalWrite(AIN1, inPin1);
    digitalWrite(AIN2, inPin2);
    analogWrite(PWMA, speed);
  }
}


void RobotPlatform::loop()
{
  if (Serial.available() > 0) {
    if (readLine()) {
      bool result = processCommand();
      if (result == false) {
        response += " ER";
      } else {
        response += " OK";
      }
      sendResponse();
      command = "";
    }
  }

  //Autonomous behaviour here, eg: collision detection etc.

  //Collision detenction
  /*
  int v;
  v = analogRead(0);

  if (v < 800) {
    setMotor(0, 0, 0);
    setMotor(1, 0, 0);
  }
  */
}



RobotPlatform rover;

void setup()
{
  rover.setup();
}

void loop()
{
  rover.loop();
  delay(100);
}
/*


int STBY = 4;

int PWMA = 6;
int AIN1 = 8;
int AIN2 = 7;

int PWMB = 11;
int BIN1 = 9;
int BIN2 = 10;

int timer = 0;
char serialIn = 's';

int rspeed = 50;

char left_wheel_speed = 0;
char left_wheel_dir   = 0; //or 1
char right_wheel_speed = 0;
char right_wheel_dir   = 0; //or 1


//left blue white, green white

//right white white, green blue

void move(int motor, int speed, int direction) {
  digitalWrite(STBY, HIGH);

  boolean inPin1 = LOW;
  boolean inPin2 = HIGH;

  if (direction == 1) {
    inPin1 = HIGH;
    inPin2 = LOW;
  }

  if (motor == 1) {
    digitalWrite(BIN1, inPin1);
    digitalWrite(BIN2, inPin2);
    analogWrite(PWMB, speed);
  } else {
    digitalWrite(AIN1, inPin1);
    digitalWrite(AIN2, inPin2);
    analogWrite(PWMA, speed);
  }
}

void stop(){
//enable standby  
  digitalWrite(STBY, LOW); 
}

void setup() {
  // put your setup code here, to run once:
  pinMode(STBY, OUTPUT);

  pinMode(PWMA, OUTPUT);
  pinMode(AIN1, OUTPUT);
  pinMode(AIN2, OUTPUT);

  pinMode(PWMB, OUTPUT);
  pinMode(BIN1, OUTPUT);
  pinMode(BIN2, OUTPUT);

  Serial.begin(9600);
}

void loop() {
  // put your main code here, to run repeatedly:
  //move(0, 100, 0);
  //move(1, 100, 0);

  //delay(1000);

  //move(0, 100, 1);
  //move(1, 100, 1);

  //delay(1000);

  
  if (Serial.available() >= 4) {
    left_wheel_speed = int(Serial.read());
    left_wheel_dir   = int(Serial.read());
    right_wheel_speed = int(Serial.read());
    right_wheel_dir = int(Serial.read());

    Serial.print("I recieved: left speed=");
    Serial.print(left_wheel_speed);
    Serial.print(" left wheel dir=");
    Serial.print(left_wheel_dir);
    Serial.print(" right wheel speed=");
    Serial.print(right_wheel_speed);
    Serial.print(" right wheel dir=");
    Serial.print(right_wheel_dir);
    Serial.println("");

    timer = 0;
  }

  if (serialIn == 'b') {
    move(0, rspeed, 0);
    move(1, rspeed, 0);
  }
  if (serialIn == 'f') {
    move(0, rspeed, 1);
    move(1, rspeed, 1);
  }
  if (serialIn == 'r') {
    move(0, rspeed, 1);
    move(1, rspeed, 0);
  }
  if (serialIn == 'l') {
    move(0, rspeed, 0);
    move(1, rspeed, 1);
  }

  if (serialIn == 's') {
    move(0, 0, 0);
    move(1, 0, 0);
  }

  if (timer > 50) {
    serialIn = 's';
    //Serial.println("Stopping");
    timer = 0;
  }

  timer += 1;
  //Serial.print(timer);
  //Serial.print(" ");
  //Serial.println(serialIn);
  delay(100);
}
*/

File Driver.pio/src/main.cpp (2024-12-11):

#include <Arduino.h>
#include <Wire.h>

#include "motor-speed-controller.h"

#include "pin-config.h"

// #define DEBUG_MESSAGES

#define FRAME_INTERVAL 50
#define EPISODE_INTERVAL 2000
#define DEBUG_INTERVAL 30

#define INTERRUPTS_PER_REV 6000
#define RPM_K 60000 / INTERRUPTS_PER_REV

#define DEVICE_ID 0x09
#define COMMAND_LENGTH 10
#define COMMAND_SET_SPEED 0x4D
#define COMMAND_SET_PWM 0x50
#define COMMAND_STOP 0x53
#define COMMAND_SET_REGISTER 0xFF

#define DATA_REGISTERY_SIZE 12

volatile byte currentCommand[COMMAND_LENGTH];
volatile int commandCounter = 0;

unsigned long now;
unsigned long frame_time;
unsigned long episode_time;
unsigned long debug_time;

MotorSpeedController motorA(AIN1, AIN2, PWMA, AENC1, AENC2);
MotorSpeedController motorB(BIN1, BIN2, PWMB, BENC1, BENC2);

volatile byte dataRegistery[DATA_REGISTERY_SIZE];
volatile int currentRegister = 0;

int decodeInt(byte char0, byte char1)
{
  return (char0 << 8) + char1;
}

void encodeInt(int input, volatile byte *out0, volatile byte *out1)
{
  *out0 = input >> 8;
  *out1 = input & 0xFF;
}

long decodeLong(byte (&arr)[4])
{
  return ((long)arr[0] << 24) |
         ((long)arr[1] << 16) |
         ((long)arr[2] << 8) |
         (long)arr[3];
}

void encodeLong(long input, volatile byte *out0, volatile byte *out1, volatile byte *out2, volatile byte *out3)
{
  *out0 = (input >> 24) & 0xFF; // Most Significant Byte
  *out1 = (input >> 16) & 0xFF;
  *out2 = (input >> 8) & 0xFF;
  *out3 = input & 0xFF; // Least Significant Byte
}

void on_frame()
{
  motorA.loop();
  motorB.loop();

  // Update the dataRegistery.
  // Registers 0 to 3: MotorA position long encoded as 4 bytes
  // Registers 4 to 7: MotorB position long encoded as 4 bytes
  // Registers 8 to 9: MotorA speed int encoded as 2 bytes
  // Registers 10 to 11: MotorB speed int encoded as 2 bytes

  encodeLong(motorA.getCurrentPosition(),
             dataRegistery + 0,
             dataRegistery + 1,
             dataRegistery + 2,
             dataRegistery + 3);

  encodeLong(motorB.getCurrentPosition(),
             dataRegistery + 4,
             dataRegistery + 5,
             dataRegistery + 6,
             dataRegistery + 7);

  encodeInt(motorA.getCurrentSpeed(),
            dataRegistery + 8,
            dataRegistery + 9);

  encodeInt(motorB.getCurrentSpeed(),
            dataRegistery + 10,
            dataRegistery + 11);
}

void on_episode()
{
  motorA.stop();
  motorB.stop();
}

void reset_episode()
{
  episode_time = millis();
}

void set_steering(int angle, int speed)
{
}

void commandSetSpeed(volatile byte command[COMMAND_LENGTH])
{
  /*  M    255   255   255   255  */
  /*  0x4D 0x00  0x00  0x00  0x00 */
  int motorASpeed = decodeInt(command[2], command[3]);
  int motorBSpeed = decodeInt(command[4], command[5]);

  reset_episode();

  motorA.setPIDSpeed(motorASpeed);
  motorB.setPIDSpeed(motorBSpeed);
}

void commandSetPWM(volatile byte command[COMMAND_LENGTH])
{
  /*  P    255   255   255   255  */
  /*  0x4D 0x00  0x00  0x00  0x00 */
  int motorASpeed = decodeInt(command[2], command[3]);
  int motorBSpeed = decodeInt(command[4], command[5]);

  reset_episode();

  motorA.stopPIDControl();
  motorA.setPWMSpeed(motorASpeed);

  motorB.stopPIDControl();
  motorB.setPWMSpeed(motorBSpeed);
}

void commandStop(volatile byte command[COMMAND_LENGTH])
{
  /*  S   */
  /* 0x53 */

  motorA.stop();
  motorB.stop();
}

void commandSetRegister(volatile byte command[COMMAND_LENGTH])
{
  /*  255  255   */
  /*  0xFF 0x00  */
  if (int(command[2]) > DATA_REGISTERY_SIZE - 1)
  {
    return;
  }
  currentRegister = command[2];
}

void interpretCommand(volatile byte command[COMMAND_LENGTH], int length)
{
  switch (command[1])
  {

  case COMMAND_SET_SPEED:
    commandSetSpeed(command);
    break;

  case COMMAND_SET_PWM:
    commandSetPWM(command);
    break;

  case COMMAND_STOP:
    commandStop(command);
    break;

  case COMMAND_SET_REGISTER:
    commandSetRegister(command);
    break;

  default:
    break;
  }
}

void wireRecieveEvent(int howMany)
{
  byte readBuffer;

  commandCounter = 0;
  while (Wire.available())
  {
    readBuffer = Wire.read();
    if (commandCounter < COMMAND_LENGTH)
    {
      currentCommand[commandCounter] = readBuffer;
      commandCounter++;
    }
  }
  interpretCommand(currentCommand, commandCounter);
}

void wireRequestEvent()
{
  Serial.println(currentRegister);
  Wire.write(dataRegistery[currentRegister]);
}

void setup()
{
  Wire.begin(DEVICE_ID);

  Wire.onReceive(wireRecieveEvent);
  Wire.onRequest(wireRequestEvent);

  // Enable the motor driver
  pinMode(STBY, OUTPUT);
  digitalWrite(STBY, HIGH);

  // Initialize motors
  motorA.setup();
  motorB.setup();

  // Stop the motors
  motorA.stop();
  motorB.stop();

  reset_episode();
}

void loop()
{
  now = millis();
  if (now - frame_time > FRAME_INTERVAL)
  {
    on_frame();
    frame_time = now;
  }

  if (now - episode_time > EPISODE_INTERVAL)
  {
    on_episode();
    reset_episode();
  }

  // Wait a little to ensure i2c bus does not fail
  delay(1);
}

// `6000 int is one rev

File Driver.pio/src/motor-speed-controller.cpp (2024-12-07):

#include "motor-speed-controller.h"

MotorSpeedController::MotorSpeedController(uint8_t inPin1, uint8_t inPin2, uint8_t pwmPin, uint8_t encoderPin1, uint8_t encoderPin2)
{
    inPin1_ = inPin1;
    inPin2_ = inPin2;
    pwmPin_ = pwmPin;

    encoderPin1_ = encoderPin1;
    encoderPin2_ = encoderPin2;

    encoder_ = new Encoder(encoderPin1_, encoderPin2_);

    corrected_direction_ = 1;

    Kp_ = 20;
    Kd_ = 12;
    Ki_ = 0;
    Ko_ = 50;

    pidControl_ = false;
    resetPID();
}

void MotorSpeedController::setup()
{
    pinMode(inPin1_, OUTPUT);
    pinMode(inPin2_, OUTPUT);
    pinMode(pwmPin_, OUTPUT);

    prevCount_ = 0;
    currentSpeed_ = 0;
}

void MotorSpeedController::loop()
{
    currentSpeed_ = encoder_->read() - prevCount_;

    prevCount_ = encoder_->read();

    if (pidControl_)
    {
        doPID();
    }
}

void MotorSpeedController::setPIDSpeed(int speed)
{
    speed = speed * corrected_direction_;
    pidControl_ = true;
    targetSpeed_ = speed;
}

void MotorSpeedController::stopPIDControl()
{
    pidControl_ = false;
    resetPID();
}

void MotorSpeedController::setPWMSpeed(int pwm)
{
    pwm = pwm * corrected_direction_;

    if (pwm < 0)
    {
        setDirection(BACKWARD);
    }
    else
    {
        setDirection(FORWARD);
    }
    setPWM(abs(pwm));
}

void MotorSpeedController::stop()
{
    pidControl_ = false;
    digitalWrite(inPin1_, HIGH);
    digitalWrite(inPin2_, HIGH);
    setPWM(0);
}

int MotorSpeedController::getCurrentSpeed()
{
    return currentSpeed_;
}

int MotorSpeedController::getCurrentPWM()
{
    return currentPWM_;
}

long MotorSpeedController::getCurrentPosition()
{
    return encoder_->read();
}

void MotorSpeedController::updatePIDParameters(int Kp, int Kd, int Ki, int Ko)
{
    Kp_ = Kp;
    Kd_ = Kd;
    Ki_ = Ki;
    Ko_ = Ko;
}

void MotorSpeedController::setReverse()
{
    corrected_direction_ = -1;
}

void MotorSpeedController::resetPID()
{
    prevInput_ = 0;
    ITerm_ = 0;
    pidOutput_ = 0;
}

void MotorSpeedController::doPID()
{
    // From https://github.com/joshnewans/ros_arduino_bridge/blob/main/ROSArduinoBridge/diff_controller.h
    long Perror;
    long output;
    int input = currentSpeed_;

    Perror = targetSpeed_ - currentSpeed_;
    output = (Kp_ * Perror - Kd_ * (input - prevInput_) + ITerm_) / Ko_;

    output += pidOutput_;

    if (output >= MAX_PWM)
    {
        output = MAX_PWM;
    }
    else if (output <= MIN_PWM)
    {
        output = MIN_PWM;
    }
    else
    {
        ITerm_ += Ki_ * Perror;
    }

    pidOutput_ = output;
    prevInput_ = input;

    setPWMSpeed(pidOutput_);
}

void MotorSpeedController::setPWM(uint8_t pwm)
{
    analogWrite(pwmPin_, pwm);
    currentPWM_ = pwm;
}

void MotorSpeedController::setDirection(bool direction)
{
    if (direction)
    {

        digitalWrite(inPin1_, LOW);
        digitalWrite(inPin2_, HIGH);
        return;
    }

    digitalWrite(inPin1_, HIGH);
    digitalWrite(inPin2_, LOW);
}

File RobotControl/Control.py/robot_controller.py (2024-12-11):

from smbus2 import SMBus
import time
import math
import logging
import motor_controller
from robot_state import Command, Telemetry, RobotState, MotorControllerState


class Bus:
    def __init__(self, i2c_busid):
        self.i2c_busid = i2c_busid
        self.i2c = None

    def open_i2c(self):
        self.i2c = SMBus(self.i2c_busid)

    def close_i2c(self):
        self.i2c.close()


class RobotController:
    def __init__(self, frequency, state: RobotState) -> None:
        self.state = state

        self.bus = Bus(i2c_busid=1)

        self.motor = motor_controller.MotorController(self.bus)

        self.frequency = frequency
        self.frame_duration = 1.0 / self.frequency

        self.wheel_base = 0.11

        self.command_map = {
            'set_motor_speed': self.command_set_motor_speed,
            'set_steering': self.command_set_steering,
            'stop_motors': self.command_stop_motors
        }

    def loop(self):
        start_time = time.time()

        try:

            self.bus.open_i2c()

            self.current_telemetry = Telemetry(
                time=time.time(),
                message="ok",
                gyro=(1, 0, 0),
                accel=(0, 0, 0),
                mag=(1, 0, 0),
                orientation=(0, 0, 0, 0),
                orientation_angles=(0, 0, 0),
                motor_controller=self.motor.get_state()
            )

            self.state.push_telemetry(self.current_telemetry)

            self.on_command(self.state.get_command())

            self.on_frame()

            self.bus.close_i2c()

        except OSError as e:
            logging.error(f"Error in RobotController Loop: {e.strerror}")

            self.current_telemetry = Telemetry(
                time=time.time(),
                message=e.strerror,
                gyro=(1, 0, 0),
                accel=(0, 0, 0),
                mag=(1, 0, 0),
                orientation=(0, 0, 0, 0),
                orientation_angles=(0, 0, 0),
                motor_controller=MotorControllerState(0, 0, 0, 0)
            )

            self.state.push_telemetry(self.current_telemetry)

        sleeptime = self.frame_duration - (time.time() - start_time)
        if sleeptime > 0:
            time.sleep(sleeptime)

    def set_steering(self, speed: float, angle: float) -> None:
        if angle == 0:
            self.motor.set_motor_speed(int(speed), -int(speed))
            return

        a_speed = angle / 90.0 * speed
        b_speed = speed - a_speed

        self.motor.set_motor_speed(int(a_speed), -int(b_speed))

    def stop(self):
        self.motor.set_motor_pwm(0, 0)

    def on_command(self, command: Command):
        if command is None:
            return

        if command.name not in self.command_map:
            logging.error(f"Unknow Command: {command}")
            return

        self.command_map[command.name](command.arguments)

    def command_set_motor_speed(self, arguments):
        try:
            self.motor.set_motor_speed(*arguments)
        except Exception as e:
            logging.error(f"command_set_motor_speed error {str(e)}")

    def command_set_steering(self, arguments):
        try:
            self.set_steering(*arguments)
        except Exception as e:
            logging.error(f"command_set_steering error {str(e)}")

    def command_stop_motors(self, arguments):
        try:
            self.motor.set_motor_pwm(0, 0)
        except Exception as e:
            logging.error(f"command_stop_motors error {str(e)}")

    def on_frame(self):
        pass

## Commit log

2021-10-12 Looking for stuff
    [BOM.ods, robot-platform-v2.fzz]
2021-10-12 Robot Driver converted to platformio
2021-10-19 Working on motor controller
    [MotorController.fzz]
2021-10-20 Updated BOM
    [BOM 2.ods]
2021-10-26 Motor driver
    [MotorDriver.kicad_pcb, MotorDriver.sch]
2021-10-26 Added Caps
    [MotorDriver.kicad_pcb, MotorDriver.sch]
2021-10-30 Added robot hat
    [RobotHat.kicad_pcb, RobotHat.sch]
2021-10-30 Completed Robot Had for RaspberryPi
    [RobotHat.kicad_pcb, RobotHat.sch]
2021-10-31 Re organizing
    [RobotHat.kicad_pcb, RobotHat.sch]
2021-11-02 Arduino runs at 5v with logic level shifter on i2c bus
    [RobotHat.kicad_pcb, RobotHat.sch]
2023-08-25 Motor encoder with pid control
2023-09-01 Forward and backward pid control and encoder
2024-12-07 Made some changed to make control more resilient to bus drop outs, and also motor stats visible
2024-12-11 Fixed choppy i2c connection and added some features
    [main.cpp]
2024-12-11 Updates to maintain compatibility with motor controller
